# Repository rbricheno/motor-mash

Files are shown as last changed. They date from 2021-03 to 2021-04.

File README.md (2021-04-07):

# The amazing Motor Mash Motor Mount!

This is a set of 3D printed parts that let you mount N20 gearmotors (a.k.a. "micro metal gearmotors") on some things like "smart car" robot kits that are designed to take TT gearmotors (the cheap ones with yellow plastic gearboxes). It provides an "upgrade path" for people with an otherwise nice robot that is stuck with yellow motors.

I used the motors with gearbox ratio 50:1 [(50:1 micro metal geamotor with extended back shaft that I used on Pimoroni store)](https://shop.pimoroni.com/products/micro-metal-gearmotor-extended-back-shaft?variant=3073681025). Don't get the "push header shims" to use with this, they won't fit.

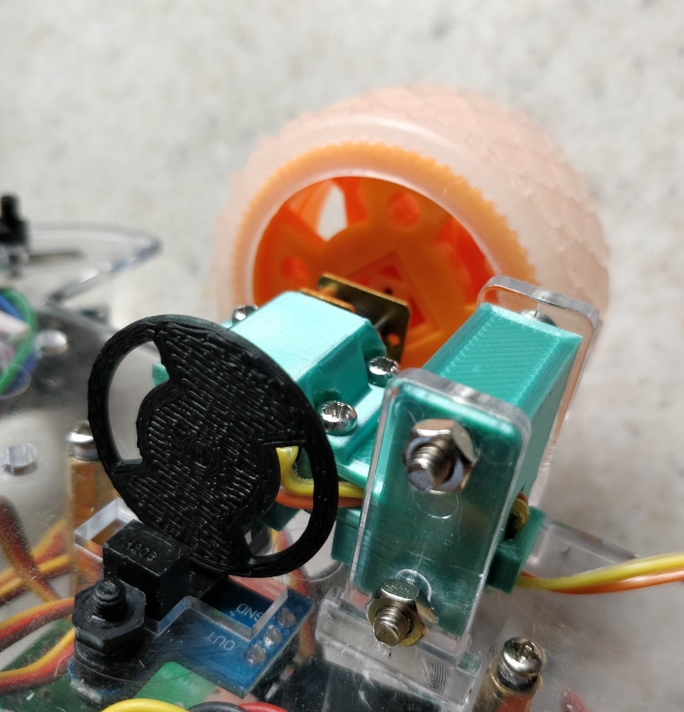
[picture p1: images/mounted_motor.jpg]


You'll need 4 M2 10mm (12mm will work) screws and 4 M2 nuts per mount to clamp the motor in place.

It's designed so you can run the wires through the middle of the mount to keep them out of the way.

The centre of the axle is the same as on a TT motor.

You'll need to mirror the `motor_mash.stl` STL and then print that and the original to get a pair of mounts, one for each side, as they aren't symetrical.

The brackets that then hold the motors in the mounts, `bottom_bracket.stl` *are* symetrical. For best results these should be printed standing on their ends, to prevent them snapping when screwed in securely.

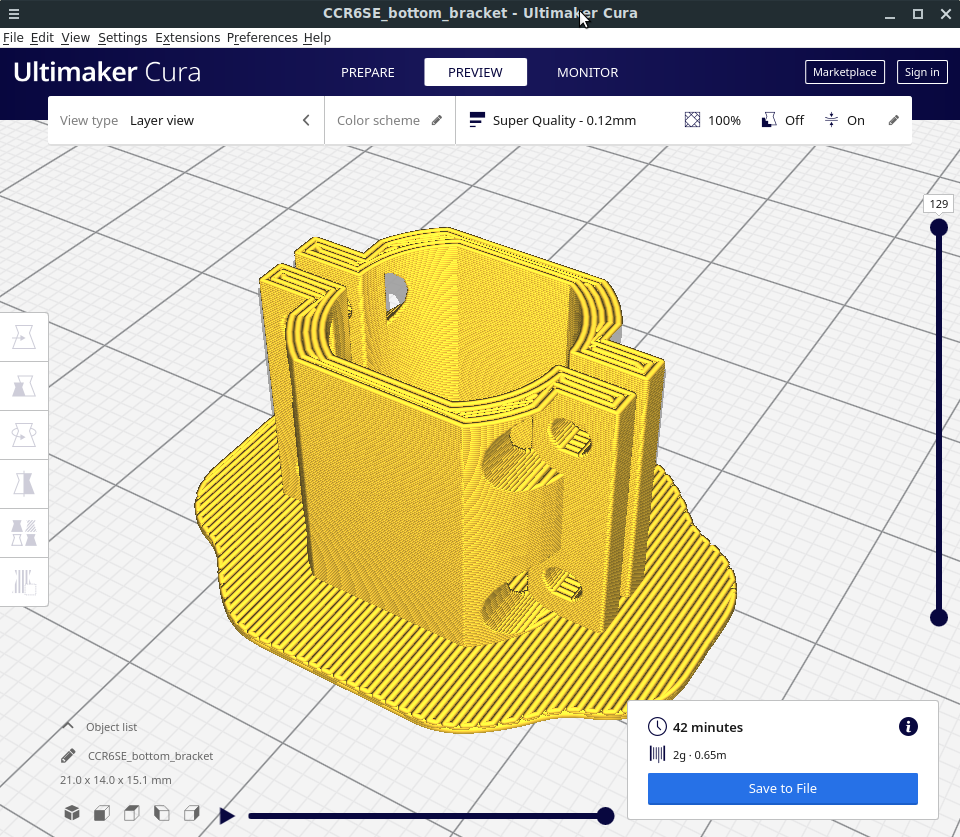
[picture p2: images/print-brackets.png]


I didn't model the "nub" on the side of the TT gearbox (yet) as my kit doesn't require that, and so for me it would only get in the way.

## Encoder wheels

Optical encoder wheels are provided, allowing you to use the same optical encoders you would have used with your yellow motors. You will need the version of the N20 motors with the extended back shaft. The extended back shaft of the N20 motor spins a lot faster than the output shaft, so I've provided the encoder wheels in two different styles. 

`n20_encoder_20.stl` is the wheel with 20 holes cut in it, which is the same pattern as the encoder wheels which norlally come with "smart car" kits. I found that this spins too fast to read, so I prefer `n20_encoder_newschool.stl` which is the same wheel but with only 2 holes in it, resulting in a 10x slower tick rate.

I found the encoder wheels that I printed did not register until I spray painted them black (a different filament may have worked fine). I also found that the placement of the wheels within the "jaws" of the encoder was very important; the wheel had to be close to one side or the other in order to register, and if it was close to the middle then it didn't work at all.

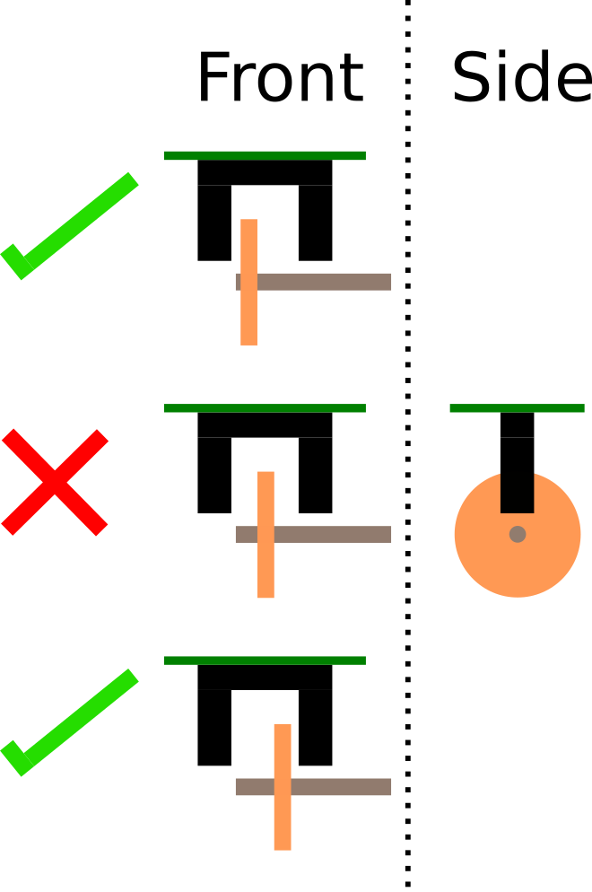
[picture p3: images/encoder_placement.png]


These should push and fit securely on the back shafts. The result looks like this:

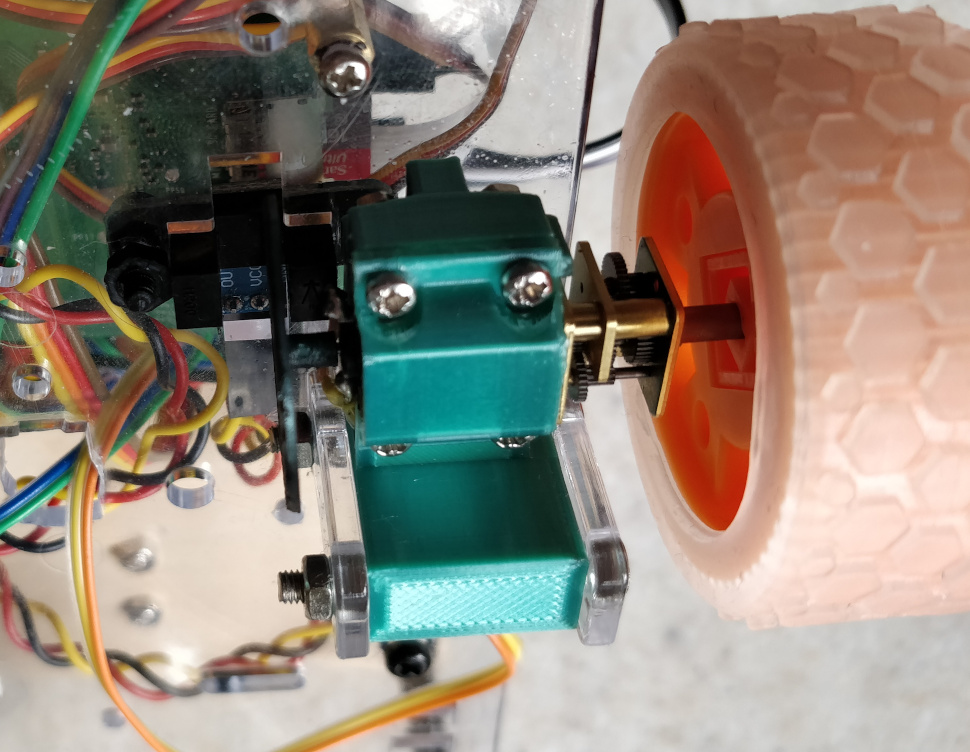
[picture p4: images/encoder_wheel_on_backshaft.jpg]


with very little little space between the sleeve of the encoder wheel and the back of the motor.

## Learn Robotics Programming

I designed these to use with the robot I was building following the instructions in the book [Learn Robotics Programming](https://www.packtpub.com/product/learn-robotics-programming-second-edition/9781839218804) by Danny Staple.

I used a [2WD smart car chassis I found on Amazon](https://smile.amazon.co.uk/gp/product/B076BPY2L3/ref=ppx_yo_dt_b_asin_title_o01_s00?ie=UTF8&psc=1) and the [N20-compatible Moon Buggy Wheels from Pimoroni](https://shop.pimoroni.com/products/moon-buggy-wheels-pair).

The settings I used in robot.py with the 50:1 motors and the newschoool encoder wheels were:
```
...
class Robot:
    wheel_diameter_mm = 48.0
    ticks_per_revolution = 200.0
    wheel_distance_mm = 130.0
...
```

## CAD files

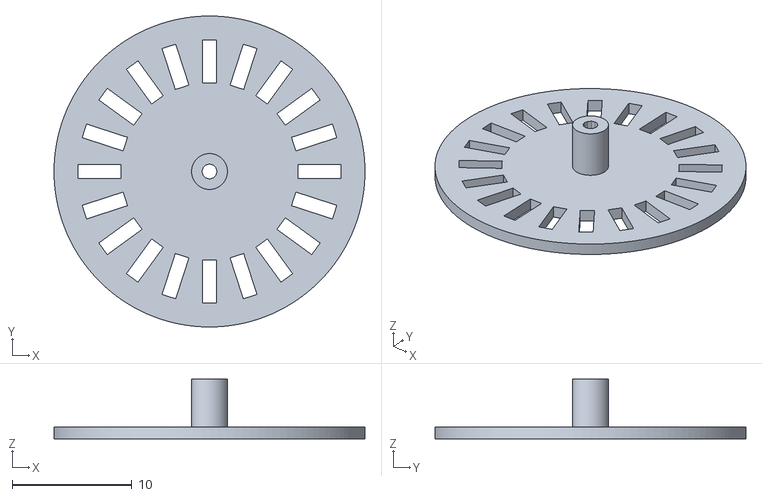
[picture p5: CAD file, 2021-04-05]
n20_encoder_20.stl
26.0 x 26.0 x 5.00

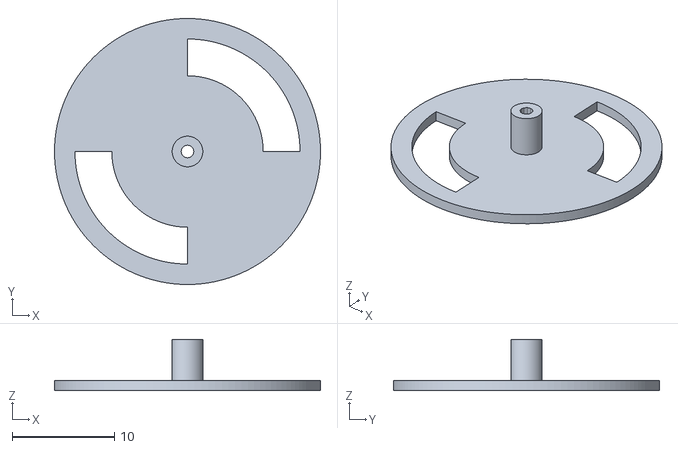
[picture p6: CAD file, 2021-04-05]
n20_encoder_newschool.stl
26.0 x 26.0 x 5.00

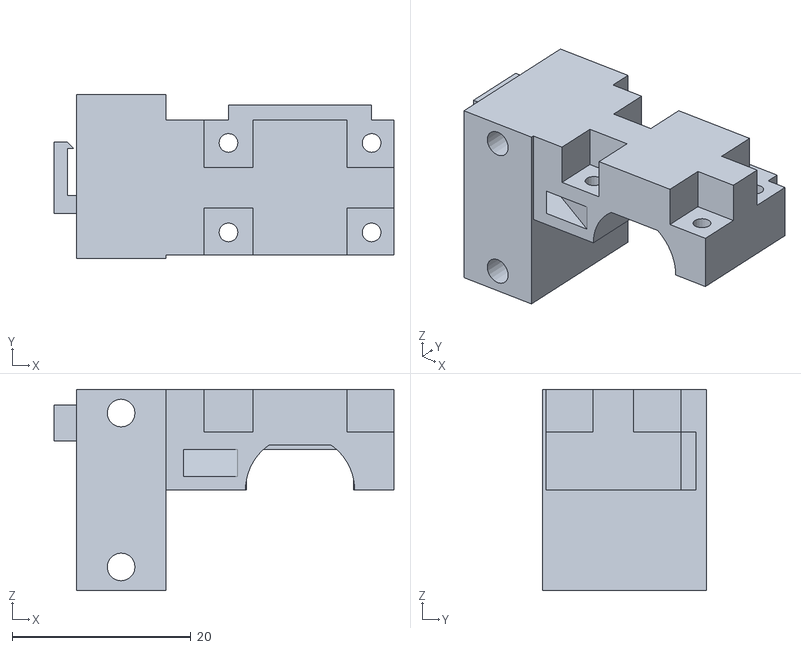
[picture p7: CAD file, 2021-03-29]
motor_mash.stl
38.0 x 18.3 x 22.5

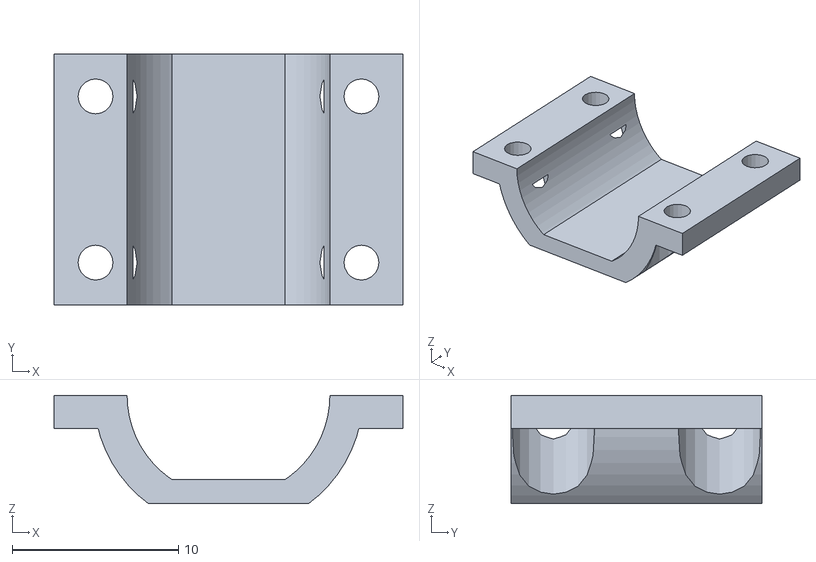
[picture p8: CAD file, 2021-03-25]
bottom_bracket.stl
21.0 x 15.1 x 6.50

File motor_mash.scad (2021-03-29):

module prism(l, w, h){
   polyhedron(
           points=[[0,0,0], [l,0,0], [l,w,0], [0,w,0], [0,w,h], [l,w,h]],
           faces=[[0,1,2,3],[5,4,3,2],[0,4,5,1],[0,3,4],[5,2,1]]
           );
}


// This is a simplified version of the main body of the motor housing

module motor() {
color("pink")

difference() {translate([0,-1.1,0]) rotate([90,0,0]) cylinder(h=15.1, d=12.2, center=true, $fn=60);


translate([-1,-1.1,8.125]) cube([20,15.1,6.15], center=true);

translate([-1,-1.1,-8.125])  cube([20,15.1,6.15], center=true);
}}




// These are the cutouts for the screw holes and the space for the nuts

module n20_mount_cutout() {

translate([25,-1.10,0])
{


translate([-8,5,0])
cylinder(h=40, d=2.1, center=true, $fn=20);

translate([8,5,0])
cylinder(h=40, d=2.1, center=true, $fn=20);

translate([-8,-5,0])
cylinder(h=40, d=2.1, center=true, $fn=20);

translate([8,-5,0])
cylinder(h=40, d=2.1, center=true, $fn=20);

translate([0,0,11.5]) {

translate([-8,5,0])
cube([5.5,5.5,10], center=true);

translate([8,5,0])
cube([5.5,5.5,10], center=true);

translate([-8,-5,0])
cube([5.5,5.5,10], center=true);

translate([8,-5,0])
cube([5.5,5.5,10], center=true);
}
}
}

//****************************************************************************

// Here begins the top part of the motor mount (the complicated bit)


// This is the little clamping feature that holds the front of the motor

difference() {
union() {
translate([25,7.3,5.5]) color("green") cube([12,1.7,2], center=true);

translate([32,7.3,3.25]) color("green") cube([2,1.7,6.5], center=true);

translate([18,7.3,3.25]) color("green") cube([2,1.7,6.5], center=true);

}

// This represents the first brass plate of the gearbox (the part which is being clamped)
translate([25,6.9,0.05]) color("pink") cube([12.2,0.92,10.1], center=true);

}


// This is a shaft that gets cut out to allow wires to pass through

module wire_shaft() {
translate([0,0,3])
rotate([0,0,-30])
cube([60,3,3], center=true);
}


// This is the large block which abuts the underside of the robot and supports the motor

difference() {
translate([22.5,-1.1,8.125 -2.5 ]) color("magenta") cube([26,15.1,6.25 + 5], center=true);
translate([25,0,0]) scale([1,2,1]) motor();

n20_mount_cutout();
wire_shaft();

}

// This is the other large block, that has the big M3 screws through it for attaching to the TT motor mount

difference() {
translate([5,0.15,0]) color("green") cube([10,18.3,22.5], center=true);

translate([5,0,8.6]) rotate([90,0,0]) cylinder(h=40, d=3.1, center=true, $fn=20);


translate([5,0,-8.6]) rotate([90,0,0]) cylinder(h=40, d=3.1, center=true, $fn=20);
wire_shaft();
}

// This is the little clip to hold the wires and provide a litle strain relief on the back

translate([-1.75,0,7.5])
cube([1.5,8,4],center=true);

translate([0,-3,7.5])
cube([2,2,4],center=true);

   translate([-0.3,3.3,9.5])
rotate([0,90,90])
   prism(4, 0.7, 0.7);

//****************************************************************************

// From here onwards is the bottom bracket

color("red")
difference() {
union() {
translate([25,0,0])
difference() {
translate([0,-1.1,0]) rotate([90,0,0]) cylinder(h=15.1, d=16.2, center=true, $fn=60);
translate([-1,-1.1,5]) cube([20,16,10], center=true);
translate([-1,-1.1,-11.5]) cube([20,16.1,10], center=true);
 scale([1,2,1]) motor();
}

translate([25,0,0])
difference() {
translate([0,-1.1,-1])
cube([21,15.1,2], center=true);
translate([0,-1.1,0]) rotate([90,0,0]) cylinder(h=16, d=12.2, center=true, $fn=60);
}

}

translate([25,-1.10,0])
{


translate([-8,5,0])
cylinder(h=40, d=2.1, center=true, $fn=20);

translate([8,5,0])
cylinder(h=40, d=2.1, center=true, $fn=20);

translate([-8,-5,0])
cylinder(h=40, d=2.1, center=true, $fn=20);

translate([8,-5,0])
cylinder(h=40, d=2.1, center=true, $fn=20);
}


translate([25,-1.10,-22])
{


translate([-8,5,0])
cylinder(h=40, d=5, center=true, $fn=20);

translate([8,5,0])
cylinder(h=40, d=5, center=true, $fn=20);

translate([-8,-5,0])
cylinder(h=40, d=5, center=true, $fn=20);

translate([8,-5,0])
cylinder(h=40, d=5, center=true, $fn=20);
}

}

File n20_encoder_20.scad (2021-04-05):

difference() {
union() {
cylinder(r=13,h=1,center=true, $fn=120);

translate([0,0,2]) 
cylinder(r=1.5,h=5,center=true, $fn=120);

}
cylinder(r=0.625,h=20,center=true, $fn=12);


for ( i = [0 : 19] ){

rotate([0,0,18 * i]) translate([0,9.2,0]) cube([1.2,3.6,3], center=true);

}

}

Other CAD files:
n20_encoder_newschool.scad

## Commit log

2021-03-25 Add first draft STLs
    [bottom_bracket.stl, motor_mash.stl]
2021-03-25 Here be dragons (and magic numbers!)
    [motor_mash.scad]
2021-03-29 Corrected placement of M3 holes. Reduced clip size.
    [motor_mash.scad, motor_mash.stl]
2021-03-29 Add optical encoder wheels for N20 motor back shaft
    [n20_encoder_20.scad, n20_encoder_20.stl, n20_encoder_newschool.scad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]
2021-04-05 Updated encoders, images for docs
    [n20_encoder_20.scad, n20_encoder_20.stl, n20_encoder_newschool.scad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]
2021-04-07 Photos of mounted motor.
2021-04-07 Add stl names
